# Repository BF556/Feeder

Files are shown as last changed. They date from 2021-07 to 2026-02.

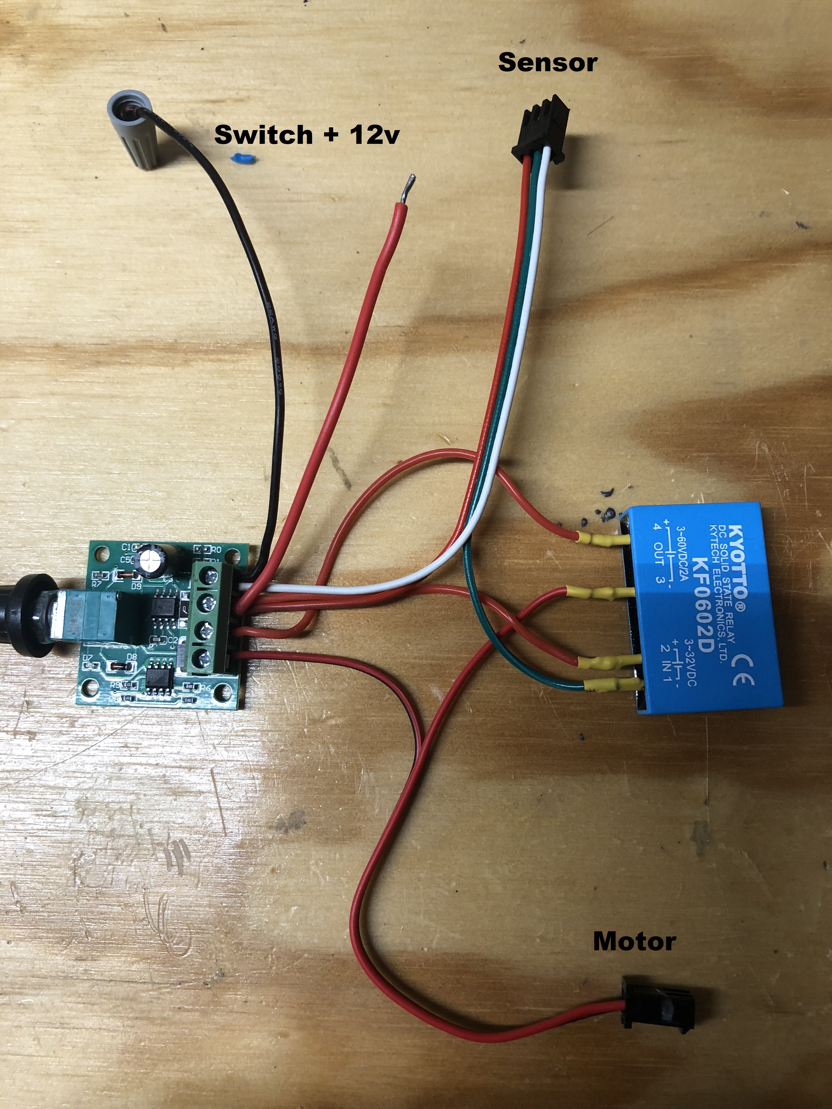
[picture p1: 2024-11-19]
Images/prox wiring.JPG

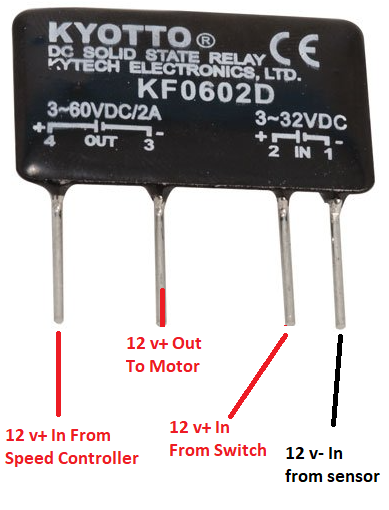
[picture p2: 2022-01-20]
Images/relay.png

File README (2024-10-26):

This work is licensed under the Creative Commons Attribution-NonCommercial 4.0 International License.

You are free to:
•	Share — copy and redistribute the material in any medium or format
•	Adapt — remix, transform, and build upon the material

Under the following terms:
•	Attribution — You must give appropriate credit, provide a link to the license, and indicate if changes were made. You may do so in any reasonable manner, but not in any way that suggests the licensor endorses you or your use.
•	NonCommercial — You may not use the material for commercial purposes.
•	No additional restrictions — You may not apply legal terms or technological measures that legally restrict others from doing anything the license permits.

To view a copy of this license, visit http://creativecommons.org/licenses/by-nc/4.0/ or send a letter to: Creative Commons, PO Box 1866, Mountain View, CA 94042, USA

Please read the manual for project details.

To download the latest design click the green "Code" button, then click "Download Zip".  In dedication of my friend Dr3wcifer.

paypal: writeus2day@yahoo.com
@bf556 on Coinbase
Bitcoin:  bc1qdez7d8wg0c6aw0pvaz97u2s23d3tlprlmmnsug
Ethereum/USDC:  0x2717F3bb693590379e953641a78d14Bf66cc5227

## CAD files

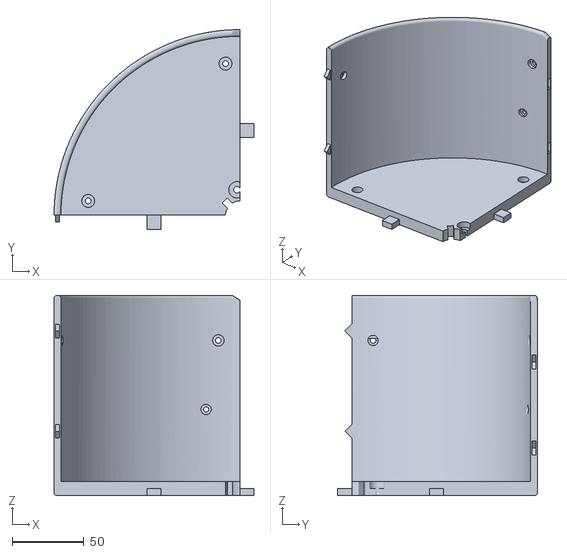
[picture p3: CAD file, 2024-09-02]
1. Main Body/Main_Body_M634JS_300mm_RB.stl
139.8 x 139.6 x 140.0

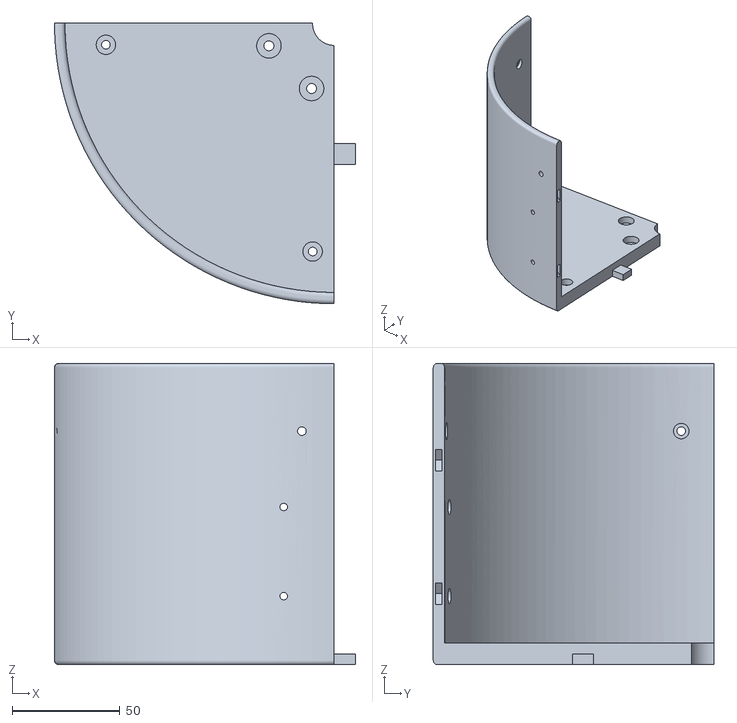
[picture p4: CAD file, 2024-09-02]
1. Main Body/Main_Body_M634JS_300mm_LB.stl
139.8 x 130.3 x 140.0

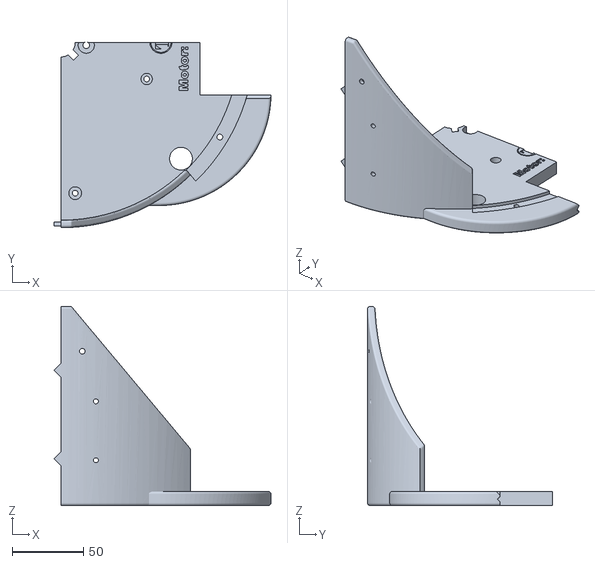
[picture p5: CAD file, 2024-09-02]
1. Main Body/Main_Body_M634JS_300mm_LF.stl
152.5 x 130.3 x 140.0

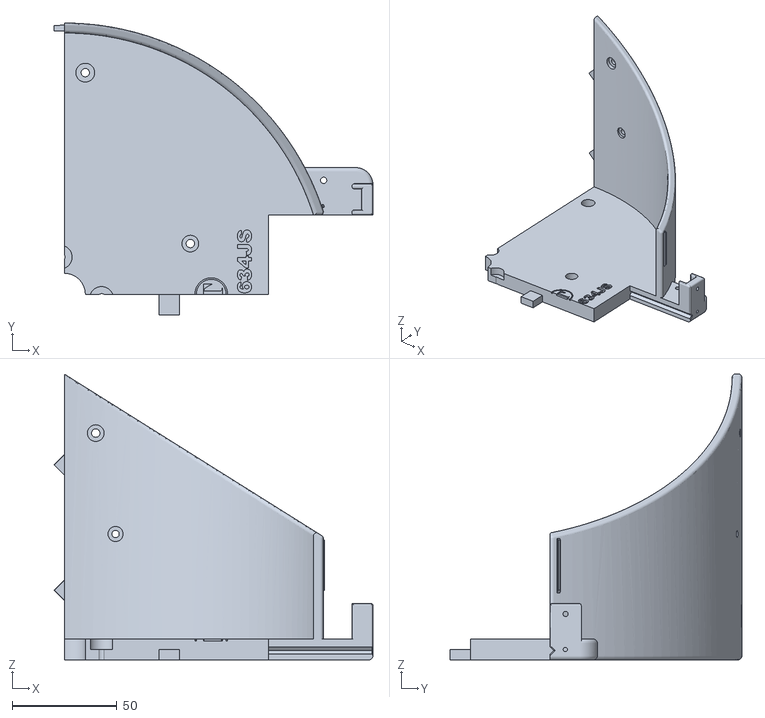
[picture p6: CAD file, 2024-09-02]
1. Main Body/Main_Body_M634JS_300mm_RF.stl
152.6 x 139.6 x 136.7

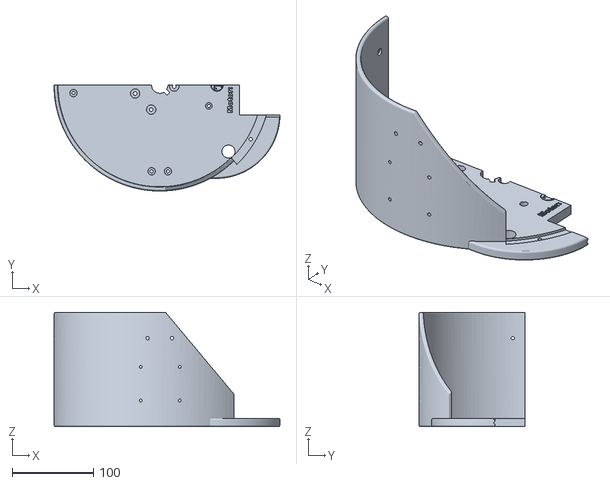
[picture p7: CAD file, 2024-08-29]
1. Main Body/Main_Body_M634JS_300mm_Left.stl
277.5 x 130.3 x 140.0

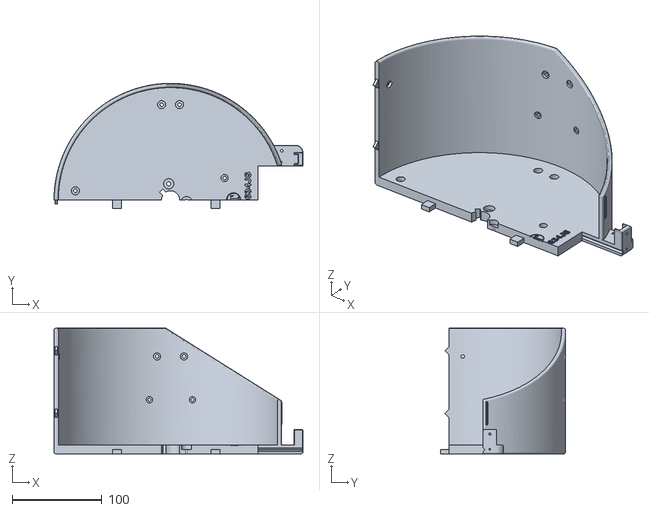
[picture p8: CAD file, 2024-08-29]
1. Main Body/Main_Body_M634JS_300mm_Right.stl
277.5 x 139.6 x 140.0

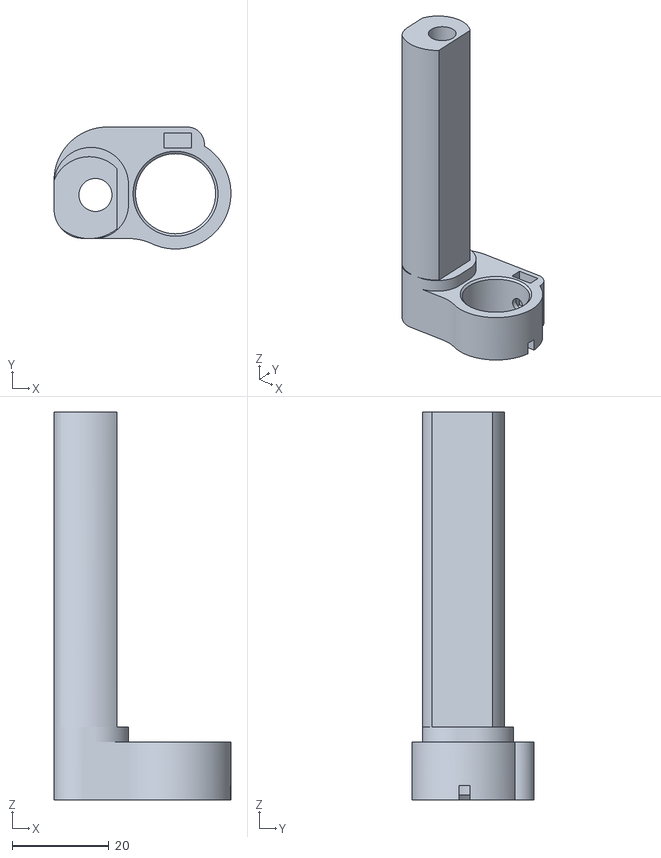
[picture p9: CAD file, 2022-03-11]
8. APP/APP_Bracket_Main.stl
36.5 x 25.1 x 80.0

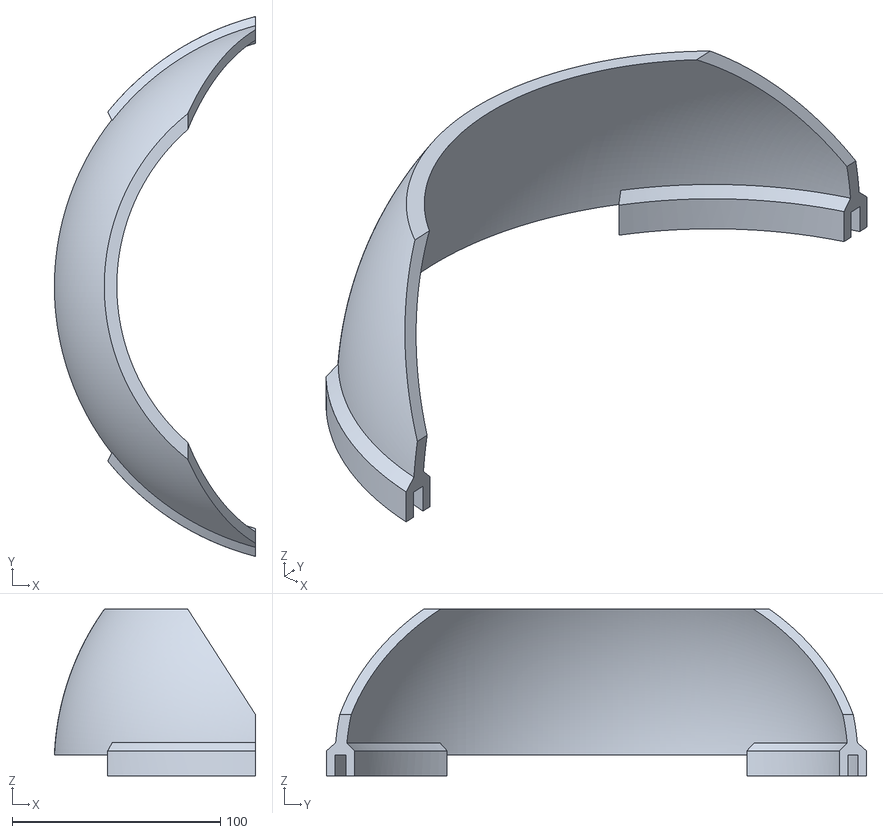
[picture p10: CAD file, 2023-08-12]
1. Main Body/Main_Body_Wall_Extender_300mm.stl
96.6 x 259.3 x 80.0

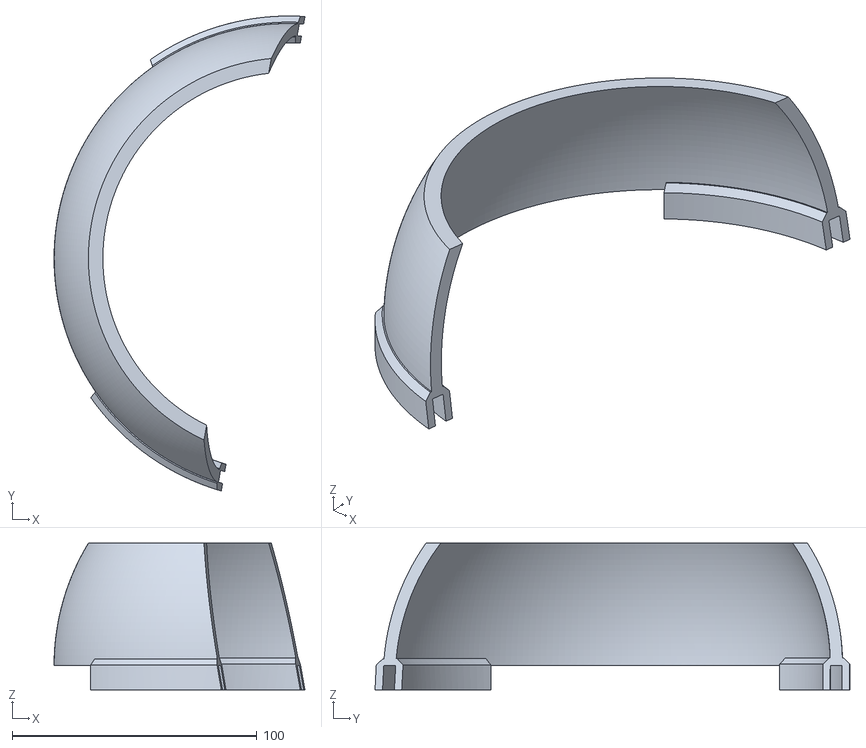
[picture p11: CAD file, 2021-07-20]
1. Main Body/Main_Body_Wall_Extender.stl
102.5 x 194.1 x 60.0

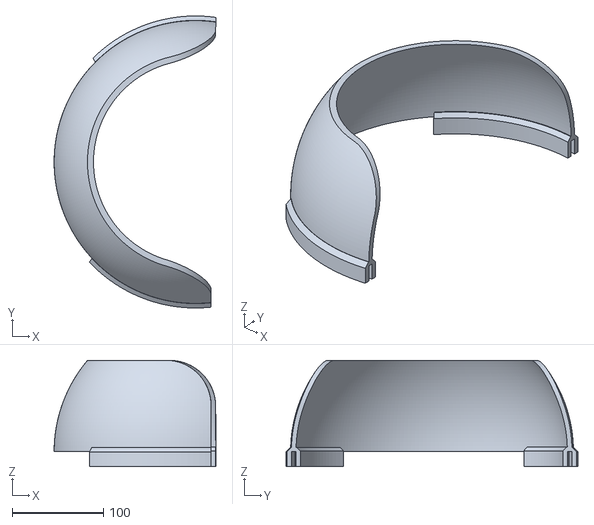
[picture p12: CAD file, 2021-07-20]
1. Main Body/Main_Body_Wall_Extender_MONGO.stl
177.3 x 320.0 x 116.5

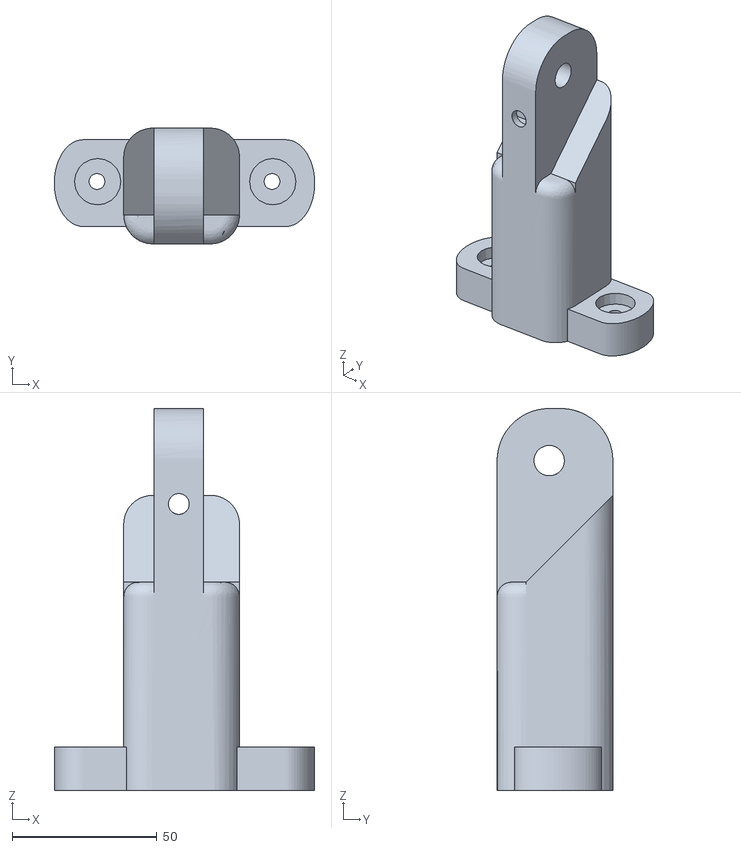
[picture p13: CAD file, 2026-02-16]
2. Mounts/Mount_Post-ASP-30x30mm.stl
90.0 x 40.0 x 132.0

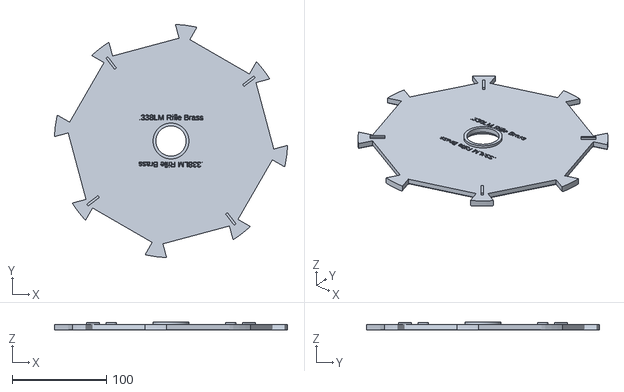
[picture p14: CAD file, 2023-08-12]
3. Collator Plates/Rifle_Brass_Collator_Plate_338LM_300mm.stl
247.2 x 247.2 x 8.50

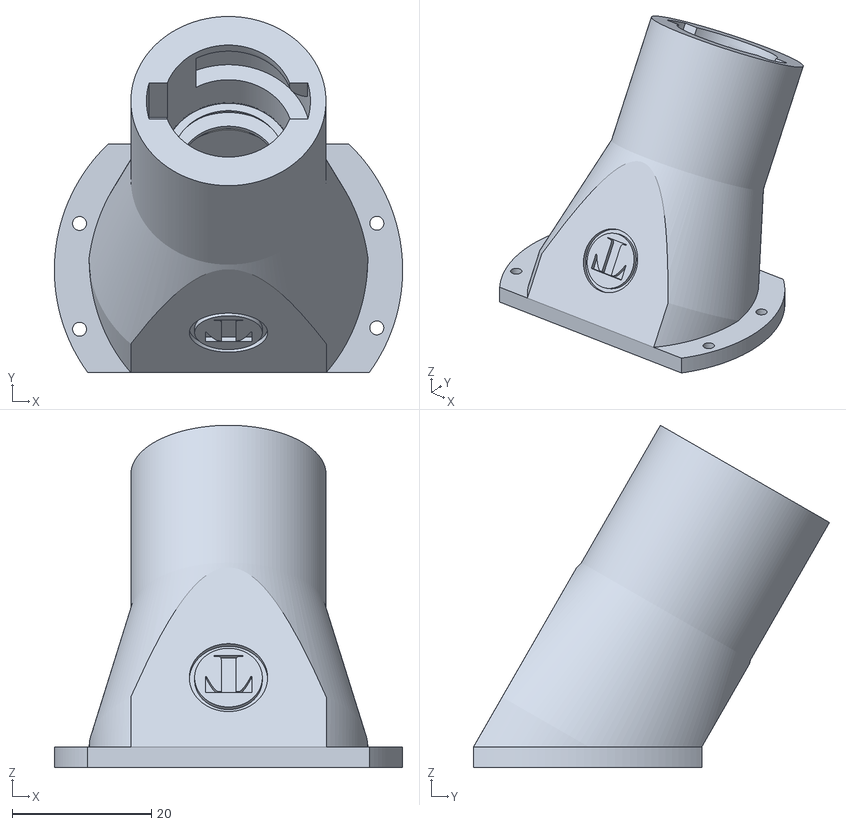
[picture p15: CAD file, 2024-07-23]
4. Slide Plates/Brass_Drop_Hole_Adapter.stl
50.0 x 51.1 x 49.1

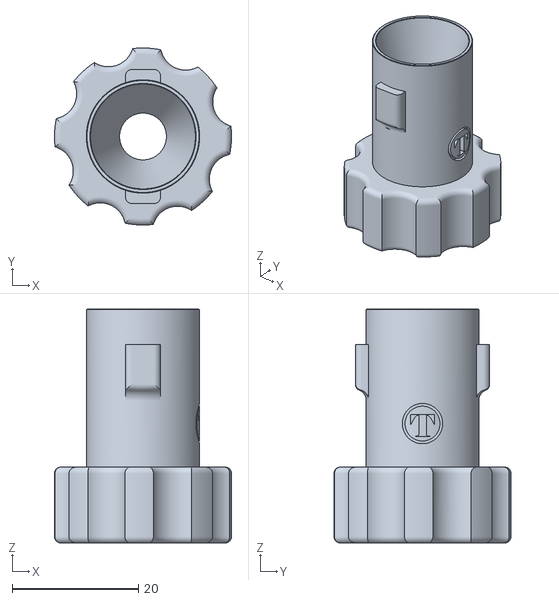
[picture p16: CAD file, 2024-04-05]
5. Adapters/Lee_Tube_Adapter_1_Funnel.stl
28.0 x 28.0 x 37.0

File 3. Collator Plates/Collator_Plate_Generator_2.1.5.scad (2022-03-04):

//*** COLLATOR PLATE GENERATOR ***///
//***   (c) AmmoMike83  ***///
//*** Mods by RedLegEd / TylerR  ***///
/*
*** INSTRUCTIONS ***
- download openSCAD http://www.openscad.org/downloads.html
- modify options
- press F5 for preview
- press F6 to render
- press F7 to export to stl
*/

//  ###########################################################
//  ##############   See Examples at bottom   #################
//  ###########################################################

//  ###########################################################
//  ###############     Options to Customize   ################
//  ###########################################################

// PLATE DIAMETER - 179.5mm(Small)/247.5mm(Medium)/297mm(Mongo)
collator_plate_d=179.5; 

// MAIN OPTIONS
description="Large Pistol Bullet (#7)"; //description
caliber=11.5; //ENTER YOUR CALIBER HERE
collator_plate_h=15; //plate height - pistol 15, rifle 18

// LONG RIFLE BULLETS
isLongRifleBullet = false; // Used for very long rifle bullets
addRamps = true; // Ramps give more angle for better feeding
squareSlotDepth = 1.5; //Depth of square bullet slot

// RIFLE BRASS PLATE OPTIONS
// Use caliber setting for hole length
isRifleBrassPlate = false; // Use with Rifle Brass  
rifleHoleWidth = 12; // Set to brass width

// PLATE OPTIONS
addPivots = false;  // Add pivots for base down brass feeding
addSlides = false;  // Add sliding slots for bullets
addSideSlides = true;  // Add sliding slots on the side of hole
slideDepth = 5.2;  // Depth of slides
slideLength = 15; // Length of slide
addRidges = true;  // Add top ridges for brass plates
ridgeCenter = true; // if false ridges align with far side of hole
ridgeAlternate = true; // Skip every other hole
ridgeHeight = 2.0; // Ridge height in mm
ridgeLength = 15; // Ridge length in mm
ridgeAngle =30; // Angle the ridges

addBevel = true;  // Add top bevel to holes
bevelSize = 1.55; // Change depth of bevel (1.3 - 1.6)
hole_multiplier=1.6; // Modify the number of holes

// SHAFT SLIP CLUTCH
useClutch = true;  // Set to true to use slip clutch

// SHAFT OPTIONS (HEX)
useHex = false;  // Set true if using hex shaft
addHexHandle = true; // Adds hex handle to top of plate
hexHandleHeight = 5; // Set height of hex handle
addHexScrewSlot = true;  // Adds slot to shaft for set screw
setScrewOnFlat = true; //  Set screw on corner or flat
hxw=12.4;  // Hex Hole Width

// SHAFT OPTIONS (STANDARD)
shaft_hole=9.5; //shaft hole
shaft_slot_length=28;
shaft_slot_width=4.5;

// Other
$fn=100; //resolution 50-100 is fine
bullet_caliber=caliber+1.0; //caliber in (mm) + 1.0 to 1.5 mm

// ####### Customize Here ########
/*
description=".300 AAC Blackout";
collator_plate_d=247.5;
caliber=36;
collator_plate_h=6;
isRifleBrassPlate = true;
rifleHoleWidth = 9;
hole_multiplier=.68;
ridgeLength = 20;
*/



//  ###########################################################
//  #############     Do Not Change Code Below   ##############
//  ###########################################################

// MAIN Routine
difference() {
union(){
                
    collator_plate();

    if(addPivots) {
        for(p=[.01:360/round(360/bullet_caliber/hole_multiplier):359]){pivot(p+15);}
    }  
  
    if(addRidges) {
        if(ridgeAlternate) {
            for(p=[0:360/round(360/bullet_caliber/hole_multiplier)*2:359]){ridges(p+15);}
        } else {
            for(p=[0:360/round(360/bullet_caliber/hole_multiplier/1):359]){ridges(p+15);}
        }
    
}
 
    if(isLongRifleBullet) {
        for(p=[0:360/round(360/bullet_caliber/hole_multiplier):359]){roundedEdge(p+15);}
    }
}

    if(isLongRifleBullet) { 
        for(p=[0:360/round(360/bullet_caliber/hole_multiplier):359]){       squareBuletHole(p+15);}
    }   
    
   
}

//  ###########################################################
module ramps(z) {
    
    z=z-2;
               translate([((collator_plate_d/2)*cos(z-caliber/2-3)),((collator_plate_d/2)*sin(z-caliber/2-3)),(collator_plate_h/2-.1)]) rotate([0,0,z+166])    prism(bullet_caliber, hole_multiplier*5, 3); 
    
}

//  ###########################################################
module squareBuletHole(z) {
    
      //Square
     translate([((collator_plate_d/2-bullet_caliber/2)*cos(z)),((collator_plate_d/2-bullet_caliber/2)*sin(z)),0]) rotate([0,0,z]) 
    cube([bullet_caliber*squareSlotDepth, bullet_caliber, collator_plate_h*2], center=true);
    
     //Bottom Bevel
     translate([((collator_plate_d/2-bullet_caliber/2+2.5)*cos(z)),((collator_plate_d/2-bullet_caliber/2+2.5)*sin(z)),-collator_plate_h/2-(bullet_caliber/14)]) rotate([45,0,z]) 
     cube([bullet_caliber*2+.5, bullet_caliber, bullet_caliber], center=true);

     translate([((collator_plate_d/2-bullet_caliber+3)*cos(z)),((collator_plate_d/2-bullet_caliber+3)*sin(z)),-collator_plate_h/2-(bullet_caliber/14)]) rotate([0,45,z]) 
      cube([bullet_caliber+2, bullet_caliber, bullet_caliber+5], center=true);
    
    // Angled Sliding Slot
     x = z-(bullet_caliber+(caliber/1)-(caliber-hole_multiplier))-2;
     translate([((collator_plate_d/2-(bullet_caliber/2-1.9))*cos(x)),((collator_plate_d/2-(bullet_caliber/2-1.9))*sin(x)),(collator_plate_h/2)+(bullet_caliber/2.5)*bevelSize/bullet_caliber+bullet_caliber+1.2]) rotate([50+hole_multiplier,1,x+7]) cube([bullet_caliber+1,10, 30+caliber*2], center=true);////////////
    
    if(isLongRifleBullet) { 
      y = z-(bullet_caliber/2)-(bullet_caliber/15);
    //translate([((collator_plate_d/2-bullet_caliber/2-30)*cos(y-3)),((collator_plate_d/2-bullet_caliber/2-30)*sin(y-3)),(collator_plate_h/2)+(bullet_caliber/3)*bevelSize]) rotate([0,-75,y])  cube([bullet_caliber+1,9, 40+caliber*2], center=true);
        
        translate([((collator_plate_d/2-bullet_caliber/2-30)*cos(y-2.2)),((collator_plate_d/2-bullet_caliber/2-30)*sin(y-2.2)),(collator_plate_h/2)+(bullet_caliber/3)*bevelSize]) rotate([0,-84,y])  cylinder(d2=bullet_caliber/2, d1=bullet_caliber-0,h=54.1,center=true);
        
        
    }
}

//  ###########################################################
module pivot(p){
    cube = 4;
    translate([((collator_plate_d/2-bullet_caliber-1)*cos(p)),((collator_plate_d/2-bullet_caliber-1)*sin(p)),-1]) rotate([0,60,p]) cube ([cube,1.5,cube], center=true);}
    
 //  ###########################################################   
module ridges(p) {

    if(isRifleBrassPlate) { 
        p=p+360/round(360/bullet_caliber/hole_multiplier)/2;
         translate([((collator_plate_d/2-ridgeLength/2-12)*cos(p)),((collator_plate_d/2-ridgeLength/2-12)*sin(p)),collator_plate_h/2]) rotate([-ridgeAngle,-90,p]) cube ([ridgeHeight*2,2.5,ridgeLength], center=true); 
        
        } else {
            
        if(ridgeCenter) {
             p=p+(360/round(360/bullet_caliber/hole_multiplier)/2)-.5;
         translate([((collator_plate_d/2-ridgeLength/2-3)*cos(p)),((collator_plate_d/2-ridgeLength/2-3)*sin(p)),collator_plate_h/2]) rotate([-ridgeAngle,-90,p]) cube ([ridgeHeight*2,2.5,ridgeLength], center=true); 
        
        }  else {
            p = p+(bullet_caliber/2)-(bullet_caliber/15)+.5;
            translate([((collator_plate_d/2-ridgeLength/2-.3)*cos(p)),((collator_plate_d/2-ridgeLength/2-.3)*sin(p)),collator_plate_h/2]) rotate([0,-90,p]) cube ([ridgeHeight*2,2.5,ridgeLength], center=true); 
        }
    }
}  

//  ###########################################################
module roundedEdge(p) {

     z = p-(bullet_caliber+(caliber/1.0)+0);
    
    union() {
     difference(){
        union() {

     mf = 2-caliber/15;       
             translate([((collator_plate_d/2-bullet_caliber/2-mf)*cos(z)),((collator_plate_d/2-bullet_caliber/2-mf)*sin(z)),bullet_caliber/2-caliber-3]) rotate([-12,90,z]) cylinder(d=bullet_caliber*4.6,h=bullet_caliber+5.9, center=true);
            
        }

        translate([((collator_plate_d/2-bullet_caliber/2)*cos(z-6.5)),((collator_plate_d/2-bullet_caliber/2)*sin(z-6.5)),bullet_caliber/2-9]) rotate([-15,90,z]) cube ([bullet_caliber*5,bullet_caliber*3+10,bullet_caliber*4],center=true);

      translate([0, 0, -collator_plate_h-10 ]) cylinder(d=collator_plate_d+10,h=collator_plate_h+20, center=true) ;
        
         translate([0, 0, collator_plate_h ])  cylinder(d=collator_plate_d+10,h=collator_plate_h, center=true) ;

    }
      // ##### LONG RIFLE ######
            if(isLongRifleBullet && addRamps) {
           for(z=[0:360/round(360/bullet_caliber/hole_multiplier):359]){ramps(z+15);}
         }
    }
}
    
//  ###########################################################
module collator_plate(){
    difference(){
        //plate
        union() {
            
            
            cylinder(d=collator_plate_d,h=collator_plate_h, center=true) ;
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

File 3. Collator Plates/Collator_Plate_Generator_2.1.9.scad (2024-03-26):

//*** COLLATOR PLATE GENERATOR ***///
//***   (c) AmmoMike83  ***///
//*** Mods by RedLegEd / TylerR  ***///
/*
*** INSTRUCTIONS ***
- download openSCAD http://www.openscad.org/downloads.html
- modify options
- press F5 for preview
- press F6 to render
- press F7 to export to stl
*/

//  ###########################################################
//  ##############   See Examples at bottom   #################
//  ###########################################################

//  ###########################################################
//  ###############     Options to Customize   ################
//  ###########################################################

// PLATE DIAMETER - 179.5mm(Small)/247.5mm(Medium)/297mm(Mongo)
collator_plate_d=179.5; 

// MAIN OPTIONS
description="Large Pistol Bullet (#7)"; //description
caliber=11.5; //ENTER YOUR CALIBER HERE
collator_plate_h=15; //plate height - pistol 15, rifle 18
hole_multiplier=1.6; // Modify the number of holes

// PLATE OPTIONS
addBevel = true;  // Add top bevel to holes
bevelSize = 1.55; // Change depth of bevel (1.3 - 1.6)

// RIFLE BRASS PLATE OPTIONS
// Use caliber setting for hole length
isRifleBrassPlate = false; // Use with Rifle Brass  
rifleHoleWidth = 12; // Set to brass width

// Ridge Options
addRidges = true;  // Add top ridges for brass plates
ridgeCenter = true; // if false ridges align with far side of hole
ridgeAlternate = true; // Skip every other hole
ridgeAlternateNum = 2; // Set how ofter the ridges occur
ridgeHeight = 2.0; // Ridge height in mm
ridgeLength = 15; // Ridge length in mm
ridgeWidth = 2.5; // Ridge width in mm
ridgeAngle = 30; // Angle the ridges
ridgePosition = 0; // Position of the ridges
ridgeInsidePosition = 3; // Inside position of the ridges

// Slide Options
addSlides = false;  // Add sliding slots for bullets
//slideDepth = 1;  // Depth of slides
//slideLength = 50; // Length of slides
//slideSize = 1; // Diameter of slides
//slidePosition = 0;  //Position of slides
//slideAngle = 0;

addSideSlides = true;  // Add sliding slots on the side of hole
slideDepth = 2.0;  // Depth of slides
slideLength = 12; // Length of slides
slideSize = 1.0; // Diameter of slides
slidePosition = -6;  //Position of slides
slideAngle = 10;
slideAngle2 = 0;

// Ramp Options
addRamps = false; // Ramps give more angle for better feeding
rampHeight = 3.0;
rampLength = 7;
rampWidth = 3.5;
rampPosition = .9;
rampAngle = 4.5;
rampTopStart = 0;
rampTopLength = 1;
rampTopWidth = 2;
rampW0 = -.7;
rampW1 = .34;

// Pivot Options
addPivots = false;  // Add pivots for base down brass feeding
pivotPosition = 15;
pivotSize = .6;
pivotHeight = 1.2;
pivotWidth = 1;

// LONG RIFLE BULLETS
isLongRifleBullet = false; // Used for very long rifle bullets
squareSlotDepth = 1.5; //Depth of square bullet slot
roundedEdgeHeight = 4.9;
roundedEdgeWidth = 4.5;
roundedEdgePosition = 0;
roundedEdgeCut = 6.9;
roundedEdgeAngle = 0;
roundedEdgeSlotHeight = 0;

angledSlotHeight = 4.57;
angledSlotWidth = 1.7;
angledSlotLength = 0;
angledSlotPosition = 5.4;
bottomBevelDepth = 1.5;
bottomBevelHeight1 = -1;
bottomBevelHeight2 = 0;

// SHAFT SLIP CLUTCH
useClutch = true;  // Set to true to use slip clutch

// SHAFT OPTIONS (HEX)
useHex = false;  // Set true if using hex shaft
addHexHandle = true; // Adds hex handle to top of plate
hexHandleHeight = 5; // Set height of hex handle
addHexScrewSlot = true;  // Adds slot to shaft for set screw
setScrewOnFlat = true; //  Set screw on corner or flat
hxw=12.4;  // Hex Hole Width

// SHAFT OPTIONS (STANDARD)
shaft_hole=9.5; //shaft hole
shaft_slot_length=28;
shaft_slot_width=4.5;

// Other
$fn=100; //resolution 50-100 is fine
bullet_caliber=caliber+1.0; //caliber in (mm) + 1.0 to 1.5 mm

// ####### Customize Here ########

description="Small Brass Base Up"; 
collator_plate_d=248.0;
caliber=10.5;
collator_plate_h=20; 

addPivots = true;
pivotPosition = 15;
pivotSize = 4.9;
pivotHeight = 1.2;
pivotWidth = 1.4;

addSlides = false;
hole_multiplier=1.1;
bevelSize = 1.65;
ridgeAlternate = true;
ridgeLength = 15;
ridgeAngle = 30;
slideDepth = 4.5;
slideLength = 15; 

addSideSlides = true;
slideDepth = 1.0; 
slideLength = 18; 
slideSize = 1.5;
slidePosition = -4.0; 
slideAngle = -15;
slideAngle2 = -6;



//  ###########################################################
//  #############     Do Not Change Code Below   ##############
//  ###########################################################

// MAIN Routine  
//collator_plate();

union(){
    difference() {
        union(){
            collator_plate();
            if(addRidges && ridgeAlternate) {
                for(p=[0:360/round(360/bullet_caliber/hole_multiplier)*ridgeAlternateNum:359]){ridges(p+15);} 
            }
            for(z=[0:360/round(360/bullet_caliber/hole_multiplier):359]){
                if(addRidges && !ridgeAlternate) {ridges(z+15);} 
                if(isLongRifleBullet) {roundedEdge(z+15);}
                if(addRamps) {ramps(z+15);}
            }   
        }
        if(isLongRifleBullet) {
            for(z=[0:360/round(360/bullet_caliber/hole_multiplier):359]){
                squareBuletHole(z+15);
            }
        }
    }   
    if(addPivots) {
        for(z=[0:360/round(360/bullet_caliber/hole_multiplier):359]){
            pivot(z+pivotPosition);
        }
    }
}


//  ###########################################################
module ramps(z) {
    
    z=z-rampPosition;
    
    translate([((collator_plate_d/2)*cos(z-caliber/2-3)),((collator_plate_d/2)*sin(z-caliber/2-3)),(collator_plate_h/2)]) 
        rotate([0,0,z+166+rampAngle])    
        prism(rampLength, rampWidth, rampHeight); 
    
}

//  ###########################################################
module squareBuletHole(z) {

      //Square
     translate([((collator_plate_d/2-bullet_caliber/2)*cos(z)),((collator_plate_d/2-bullet_caliber/2)*sin(z)),0]) rotate([0,0,z]) 
        cube([bullet_caliber*squareSlotDepth, bullet_caliber, collator_plate_h*3], center=true);
    
     //Bottom Bevel
     translate([((collator_plate_d/2-bullet_caliber/2+2.4)*cos(z)),((collator_plate_d/2-bullet_caliber/2+2.4)*sin(z)),-collator_plate_h/2+bottomBevelHeight1]) rotate([45,0,z]) 
        cube([bullet_caliber*bottomBevelDepth, bullet_caliber, bullet_caliber], center=true);

 //Bottom Bevel
   //  translate([((collator_plate_d/2-bullet_caliber/2+2.4)*cos(z)),((collator_plate_d/2-bullet_caliber/2+2.4)*sin(z)),-collator_plate_h/2]) rotate([45,0,z*1.5]) 
    //    cube([bullet_caliber*bottomBevelDepth, bullet_caliber, bullet_caliber], center=true);

//translate([((collator_plate_d/2-bullet_caliber+3)*cos(z)),((collator_plate_d/2-bullet_caliber+3)*sin(z)),-collator_plate_h/2-(bullet_caliber/20)]) rotate([0,45,z])


     translate([((collator_plate_d/2-bullet_caliber+3)*cos(z)),((collator_plate_d/2-bullet_caliber+3)*sin(z)),-collator_plate_h/2+bottomBevelHeight2]) rotate([0,45,z]) 
       cube([bullet_caliber+.5, bullet_caliber-.1, bullet_caliber+5], center=true);
    
    // Angled Sliding Slot
     //x = z-(bullet_caliber+(caliber/1)-(caliber-hole_multiplier))-2;
    x = z + angledSlotPosition ;
     translate([((collator_plate_d/2-(bullet_caliber/2-2.0))*cos(x)),((collator_plate_d/2-(bullet_caliber/2-2.0))*sin(x)),(collator_plate_h/2)+(bullet_caliber/2.5)*bevelSize/bullet_caliber+bullet_caliber+angledSlotHeight]) rotate([40+hole_multiplier,-1,x+5])
        cube([bullet_caliber+angledSlotWidth,10, 30+caliber+angledSlotLength*2], center=true);////////////

    // Add slide slot
      if(addSlides) {
        
        p = z + slidePosition;     
        translate([((collator_plate_d/2-bullet_caliber/2-25)*cos(p)),((             collator_plate_d/2-bullet_caliber/2-25)*sin(p)),collator_plate_h/2-slideDepth+5])    rotate([0,-90+slideAngle,p-slideAngle2])
         
        cylinder(d2=bullet_caliber/2, d1=bullet_caliber+slideSize,h=slideLength,center=true);

    }
          
}
//  ###########################################################
module roundedEdge(p) {

     z = p-(bullet_caliber+(caliber/1.0))+roundedEdgePosition;

difference(){
  union() {
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

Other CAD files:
6. Drop Tubes/Drop_Tube_9mm.stl
7. Bullet Feed Dies/Feed_Die_6.5G_Insert.stl
8. APP/APP_Spring_APP_Insert_XL.stl
1. Main Body/Drop_Hole_Adapter.stl
1. Main Body/Drop_Hole_Adapter_Angled.stl
1. Main Body/Drop_Hole_Adapter_Angled_Body.stl
1. Main Body/Drop_Hole_Adapter_Angled_Slide.stl
1. Main Body/Drop_Hole_Adapter_Small_Right.stl
1. Main Body/Drop_Hole_Spacer_Long.stl
1. Main Body/Drop_Hole_Spacer_Short.stl
1. Main Body/Electronics_Box_Large.stl
1. Main Body/Electronics_Box_Large_Lid.stl
1. Main Body/Electronics_Box_Large_Template.stl
1. Main Body/Electronics_Box_Small.stl
1. Main Body/Electronics_Box_Small_300.stl
1. Main Body/Electronics_Box_Small_Bottom.stl
1. Main Body/Electronics_Box_Small_Bottom2.stl
1. Main Body/Electronics_Box_Small_Lid.stl
1. Main Body/Electronics_Box_Small_MONGO.stl
1. Main Body/Electronics_Box_Small_Right.stl
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

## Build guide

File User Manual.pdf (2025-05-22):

# The HomeFree Universal Reloading System

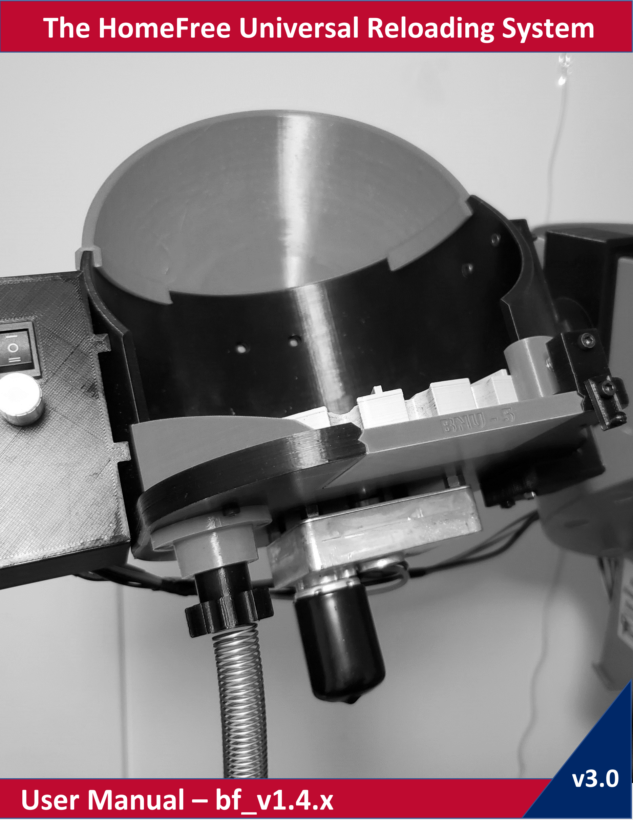
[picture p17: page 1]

v3.0

# User Manual – bf_v1.4.x

## Manual Contents

ACKNOWLEDGEMENTS | ERROR! BOOKMARK NOT DEFINED.

## PREFACE

## INTRODUCTION

Before 3D printing or engaging in this project’s dedicated thread (http://castboolits.gunloads.com/showthread.php?354324-Making-that-Bullet-Collator) on Cast Boolits, please read this user manual in its entirety as it combines the cumulative experience of numerous individuals. Ensure that the downloaded (https://www.dropbox.com/sh/xczanojq6ly3jqa/AAA5yU7iMbX_N46aC9SVfdjza) project build matches, or is higher, than the one listed on the cover page of this manual. If you would like to leave feedback on this manual, please do so here. (https://www.dropbox.com/sh/sz1o53q1a9hn4vn/AABTmmivEKmxgWxunXAH2t7Ta/User%20Manual%20Feedback%20and%20Suggestions.xlsx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)

## 3D PRINTER

A reliable 3D printer with a minimum bed size of 210mm x 210mm x 140mm, like an Ender 3, will suffice for this project. A properly calibrated 3D printer is mandatory as many parts have tight tolerances and will take hours to print. Here is a superb calibration video (https://www.youtube.com/watch?v=rp3r921DBGI) to watch before printing anything; pay close attention to the sections on frame check, (https://www.youtube.com/watch?v=rp3r921DBGI&t=166s) E-steps, (https://www.youtube.com/watch?v=rp3r921DBGI&t=422s) flow rate (https://www.youtube.com/watch?v=rp3r921DBGI&t=503s) and retraction. (https://www.youtube.com/watch?v=rp3r921DBGI&t=669s)

## FILAMENT

We recommended using PLA/PLA+ from reputable brands like Hatchbox, Overture, Sunlu, E-Sun, AMZ3D.

## TEMPERATURES

Print temperature will vary based on filament brand so feel free to experiment a little. We recommend a nozzle/bed temperature of 210˚C/60˚C as a starting point.

## NOZZLE SIZE

We recommend printing every part with a 0.4mm nozzle. While this will increase print times, it will also ensure quality parts are printed.

## PRINT SPEED

Faster prints often lead to dimensional accuracy issues, artifacts and failed prints. We recommend infill, wall and initial layer speeds of 50, 25 and 20mm/s, respectively.

## LAYER HEIGHT/INFILL/SUPPORTS/WALLS/ADHESION

All parts have their recommended print settings listed in this manual. We highly recommend following them as they have proven to yield the best quality prints.

## SLICER

We recommend Cura’s free slicing software as it has tons of print settings to play around with. Regardless, Cura’s default Standard Quality (0.2mm Layer Height) and Super Quality (0.12mm Layer Height) will suffice.

## SUB-PROJECTS

## BRASS AND BULLET COLLATOR OVERVIEW

Here is a labelled diagram of the main body with all its salient features:
A. Ramp Housing
Houses various flipping ramps.
B. Flipper Housing
Houses the flipper and sweepers.
C. Drop Hole
Hole through which brass/bullets fall.
D. Motor Mount
Secures motor to the main body.
E. Electronics Box Mount
Secures electronics box.
F. Rear Mount
Secures collator for pole mounting.
G. Right Side Mount
Secures collator for Dillon mounting.
H. Slide Plate Housing
Houses various slide plates.

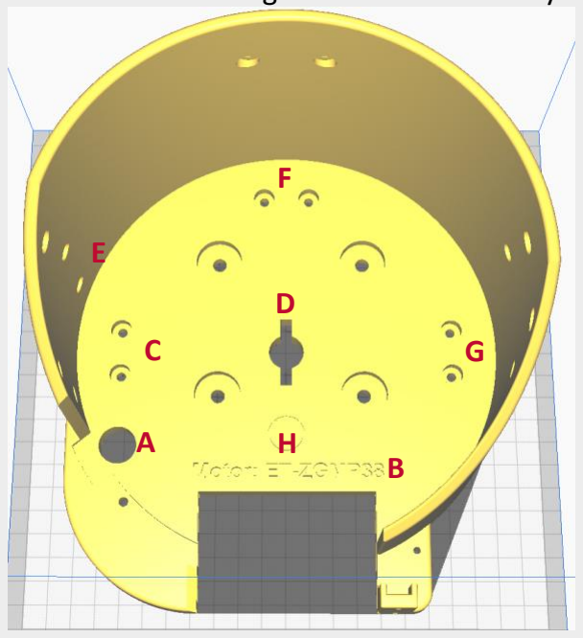
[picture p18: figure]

The following videos demonstrate all the operational capabilities of the brass and bullet collator:
- Nose up bullet collation (small bullet (https://vimeo.com/517852693)/long bullet) (https://vimeo.com/517852597)
- Nose down bullet collation (small bullet (https://vimeo.com/517852389)/long bullet) (https://vimeo.com/517852526)
- Base up brass collation (small brass) (https://vimeo.com/517852272)
- Base down brass collation (small brass (https://vimeo.com/517852848)/large brass) (https://vimeo.com/517852748)

## MONGO BRASS COLLATOR OVERVIEW

The MONGO collator has been specifically designed for large scale brass collation. Most parts from the above sub-project are compatible with the MONGO sub-project, but parts specific to this sub-project have the word MONGO attached to their filename. It should be noted that some MONGO parts require a 3D printer with a large print bed (350mm x 350mm), like an Ender 5 Plus. Here are some videos (small brass (https://vimeo.com/539431234)/large brass) (https://vimeo.com/539792171) demonstrating the operational capabilities of the MONGO brass and bullet collator.

## BULLET FEED DIES OVERVIEW

The caliber specific bullet feed dies interface directly below the drop tubes and thread directly into press toolhead with 7/8”-14 threading. Here is a video (https://vimeo.com/517848766) showing the bullet feed die in action.

## LEE APP ACCESSORIES OVERVIEW

The Lee APP accessories improve press reliability and implement the quick caliber change system for both brass and bullets. They can also work with the brass and bullet collator for super fast component processing. Here is a video (https://vimeo.com/517852456) showing the accessories in action.

## NON-3D PRINTED PARTS

Here is a comprehensive list of necessary parts by sub-project:

## BRASS AND BULLET COLLATOR

- Motor – the collator bases work with the following motors:
- 634JS (https://www.amazon.com/Greartisan-Self-Locking-Reversible-Reduction-Electric/dp/B07YBXMTWC) (recommended)
- ETZGMP38 (https://www.grainger.com/product/DAYTON-DC-Gearmotor-12VDC-52JE51)
- Switch (https://www.amazon.com/gp/product/B08Q3WJW8Q/ref=ppx_od_dt_b_asin_title_s00?ie=UTF8&psc=1) – a standard switch to power the collator unit on and off.
- Speed Controller (https://www.amazon.com/gp/product/B08XQ22F47/ref=ppx_yo_dt_b_search_asin_title?ie=UTF8&psc=1) – a motor speed controller circuit to adjust the collator plate speed.
- Power Supply (https://www.amazon.com/gp/product/B07RGHBLGC/ref=ppx_yo_dt_b_asin_title_o05_s02?ie=UTF8&psc=1) – a 12V power supply to power all the electronics.
- Female Adapter Plug (https://www.amazon.com/gp/product/B07MJ4YWQ8/ref=ppx_yo_dt_b_search_asin_title?ie=UTF8&th=1) – an adapter plug to plug in the power supply.
- JST Motor Connectors (https://www.amazon.com/gp/product/B07HN4HXZW/ref=ppx_yo_dt_b_search_asin_title?ie=UTF8&psc=1) – a set of JST connectors to connect the motor to the electronics box.
- JST Sensor Connectors (https://www.amazon.com/gp/product/B075K4HLTQ/ref=ppx_yo_dt_b_search_asin_title?ie=UTF8&th=1) – a set of JST connectors to make a wire harness for the drop tube sensors.
- Screws/Washers/Nuts (https://www.amazon.com/NINDEJIN-Socket-Screws-1060pcs-Assortment/dp/B07PHYJ8BB) – a hex nut kit with various sized bolts.
- Springs (https://www.amazon.com/dp/B0BG5W6M4Z?ref_=cm_sw_r_apan_dp_BYGXHAW4EADZJGAMCJ7N) – a spring kit with various sized springs.
- Sensors – select the parts based on the drop tube system being implementing:
- Proximity Sensor Drop Tube System
- Proximity Sensor (https://www.amazon.com/gp/product/B00TXXH4OA/ref=ppx_yo_dt_b_asin_title_o01_s00?ie=UTF8&psc=1) – a 14mm detection range normally closed (NC) inductive proximity sensor.
- Proximity Sensor (https://www.ebay.com/itm/333737317263) (Ebay) – Same as above but less expensive, slow delivery.
- Relay (https://www.amazon.com/gp/product/B00B888WVC/ref=ppx_yo_dt_b_asin_title_o00_s00?ie=UTF8&psc=1) – a 2A solid state relay.
- Photoswitch Drop Tube System (Legacy)
- Photoswitch (https://www.amazon.com/gp/product/B00XAH7DTQ/ref=ppx_yo_dt_b_asin_title_o01_s00?ie=UTF8&psc=1) – a 12V photoswitch relay circuit with a photosensor.
- LED (https://www.amazon.com/50pcs-Ultra-Bright-Diodes-Light-White/dp/B01MYYUS2R) – a 12V LED; white LEDs work best.
- Micro Switch Drop Tube System (Legacy)
- Micro Switch (https://www.amazon.com/Twidec-Straight-Switch-Action-KW11-3Z03/dp/B07P11JG8K) – a micro switch.
- Micro Switch (https://www.digikey.com/en/products/detail/honeywell-sensing-and-productivity-solutions/V7-5F17D8-336/1248546) – a more sensitive switch for light brass; trim the sides of the arm.
- Spring Tubes – choose from any of the following sizes and styles of spring tubes:
- Small/Large Spring Tube (https://www.doublealpha.biz/us/mrbulletfeeder-output-spring-and-extension-adaptor) – for feeding small rifle and large caliber brass and bullets.
- Extra Large Spring Tube (https://www.doublealpha.biz/us/double-alpha-output-chute-and-spring) – for more reliable feeding of large caliber brass and bullets.
- Multi-Diameter Spring Tube (https://tinyurl.com/ynmrh72e) – an alternative to the above spring tubes.
- Multi-Diameter Spring Tube (https://www.mcmaster.com/coil-springs/extension-spring-stock-6/) (USA) – an alternative to the above spring tubes
- Multi-Diameter Spring Tube (https://a.co/d/aAxyJWb) (USA) – another option from Amazon
- Hex Couplers (https://www.amazon.com/uxcell-Coupler-Coupling-Flexible-Connector/dp/B08M45D6F2) – a hex motor coupler alternative to pinning the motor shaft.

## BULLET FEED DIE

- Ball Bearings (https://www.amazon.com/uxcell-3-5mm-Bearing-Chromium-Precision/dp/B081SQZR62) – a set of 3.5mm ball bearings.
- Elastic bands, hooked springs (https://www.mcmaster.com/9654K964/) or O-rings.

## LEE APP ACCESSORIES

Non-3D printed parts are not required for this sub-project.

## 3D PRINTED PARTS

The project folders are numbered to reflect the build order of this manual as follows:
1. Main Body
2. Mounts
3. Collator Plates
4. Slide Plates
5. Adapters
6. Drop Tubes
7. Bullet Feed Dies
8. APP
9. Contributors - this folder contains experimental files and therefore not documented. Images – this folder contains reference images.

## IMPORTANT – PLEASE READ!

Given that this project contains over 200 files, we strongly recommend using the Parts Generator application to ensure that the correct parts are printed. While the app is not a substitute for this manual, most of the required project parts can be acquired through it. The remaining parts, which are optional and/or build specific, can be determined via this manual.

## STEP 1 – COLLATOR MAIN BODY

Part | Layer Height | Infill | Supports | Walls | Adhesion
Main Body | 0.2mm | 30% | None | 4 | None
Electronics Box | 0.2mm | 10% | None | 2 | None
All Other | 0.12mm | 10-20% | None | 2 | None

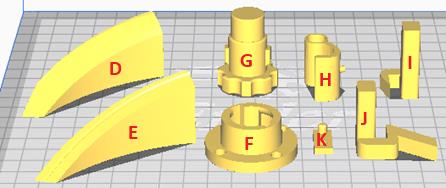
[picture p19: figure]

Main Body Folder
Part | STL File | Description
A-B | Main_Body_X | All files labelled Main_Body are used to create the collator main body.
C-X | Electronics_Box | All files labelled Electronics_Box are used to create the electronics box.
D | Ramp | This ramp rotates bullets and mounts to the ramp housing with 1 screw; this part is only used for nose up/down bullet collation.
E | Ramp_Brass_Base_Up | This ramp rotates brass and mounts to the ramp housing with 1 screw; this part it is only used for base up brass collation.
F | Drop_Hole_Adapter | This adapter allows for the quick attachment of the spring tube and mounts to the bottom of the main body’s drop hole with 4 screws.
G | Drop_Hole_Plug | This plug screws into the drop hole adapter and disables it; this part is only used for base up/down brass and nose down bullet collation.
H Flipper | | This spring-loaded flipper knocks misaligned bullets and mounts onto the flipper housing with 1 screw; a screw located on the front of the flipper housing holds the spring in place.
I | Sweeper | This sweeper arm knocks misaligned bullets and clamps onto the flipper housing; this part is only used for base up brass and long bullet collation.
J | Sweeper_Long | This sweeper arm knocks misaligned brass and clamps onto the flipper housing; this part is only used for base down rifle brass collation.
K | Slide_Plate_Latch | This latch secures slide plates and screws onto the front of the slide plate housing with 1 screw; this is an optional part.

MAIN BODY PARTS

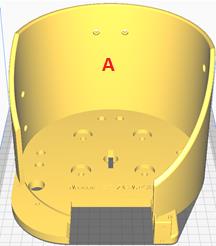
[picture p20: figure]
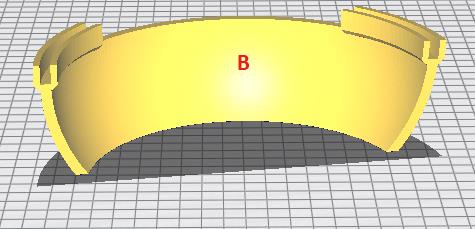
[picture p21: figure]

Part A is the collator main body and is based on the motor type being used. It requires the most time to print so ensure that the 3D printer is calibrated correctly before printing.

Part B is an optional part that friction fits to the top lip of the collator and increases collator capacity while preventing component spillage.

ELECTRONICS BOX PARTS
There are two electronics box sizes to choose from, part C-1, small and large. While the large electronics box works with any configuration of parts, we recommend the small electronics box with the proximity sensor drop tube system. The lid, part C-2, for the electronics box slides into the rear opening.

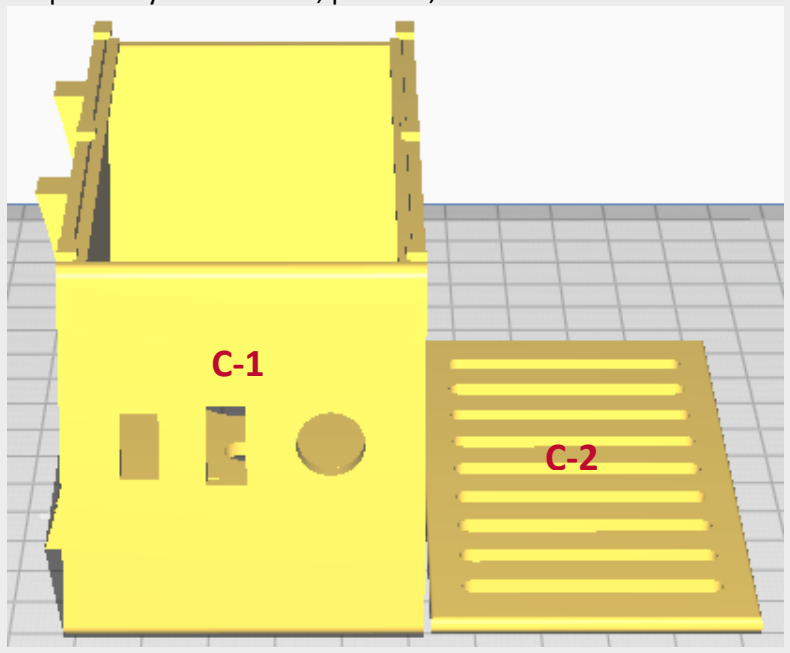
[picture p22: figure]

Files that are labelled Electronics_Box_X_Template do not have any component cut outs and allow for customization through software like Tinkercad. (https://www.tinkercad.com/)

## STEP 2 – COLLATOR MOUNTS

Part | Layer Height | Infill | Supports | Walls | Adhesion
All | 0.2mm | 30% | None | 4 | None

Mounts Folder
Part | STL File | Description
A-B | Mount_Dillon_Hang_X | These files are used to create a Dillon casefeeder mount.
C-D | Mount_Post_X | These files are used to create mounts that secure to vertical posts.
E | Mount_Square_X | These files are used to create mounts that secure to horizontal posts.
F | Thumb_Screw | This thumb screw cover is used for the adjustment screw option.

The brass and bullet collator can be mounted to a Dillon casefeeder or a circular/square post that is 1” in diameter. A 45˚ collator tilt is normally optimal, but this can vary by brass or bullet caliber.

DILLON CASEFEEDER MOUNT
A 3/8” x 1” hex bolt, washer and nut goes through the parts A and B to
control collator tilt. Be sure to insert the hex bolt before screwing the Dillon hang base to the main body. Part A mounts to the right side of the collator while part B slips over the top lip of the Dillon casefeeder.

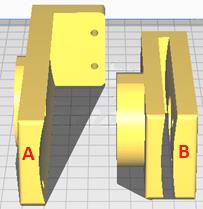
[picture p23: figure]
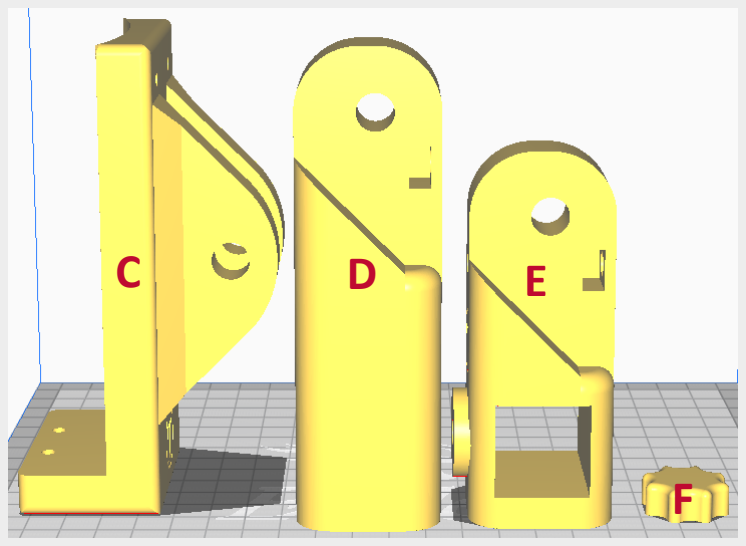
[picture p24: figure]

VERTICAL & HORIZONTAL POST MOUNTS
A 3/8” x 2 1/4” hex bolt, washer and nut goes through part C and parts D/E to control collator tilt. Part C mounts to the rear of the collator while part D slips over the top of the post being used; part D comes in two styles, one for circular posts and the other for square posts. As an alternative mounting style, part E is designed for mounting to a square horizontal post.

For those making regular changes to the collator tilt, we suggest using the adjustment screw option. A 1/4” bolt and nut can be used with parts D/E to provide an alternative to the friction fit approach of using only a hex bolt. We also recommend using part F to act as a thumb screw for the adjustment screw; see the figure on the right.

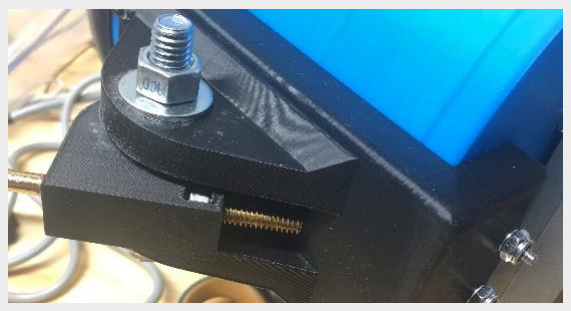
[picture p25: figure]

## STEP 3 – COLLATOR PLATES

Part | Layer Height | Infill | Supports | Walls | Adhesion
All Other | 0.2mm | 10% | None | 2 | None
Slip_Clutch_X | 0.2mm | 50% | None | 4 | None

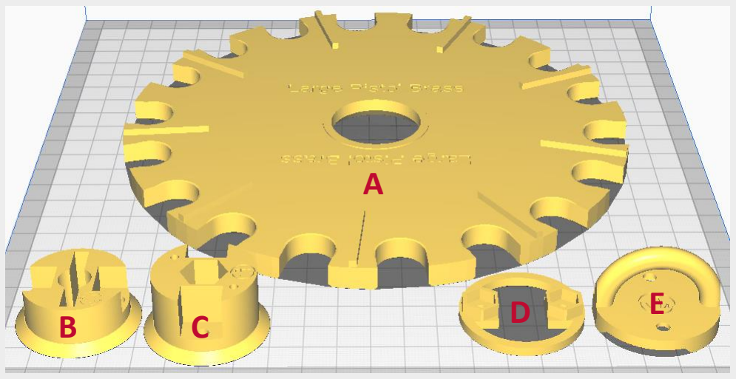
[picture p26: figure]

Collator Plates Folder
Part | STL File | Description
A X_Collator_Plate_X | | All files labelled Collator_Plate are used to create brass/bullet collator plates: • Rifle_Brass_Collator_Plate_Large.stl • a large rifle brass collator plate for base down collation. • Rifle_Bullet_Collator_Plate_Large_#4.stl • a large rifle bullet collator plate for nose up/down collation that is to be used with a nose up/down #4 slide plate.
B | Slip_Clutch_8.5mm | This clutch is for pinned motor shafts that are 8.5mm or 10mm in diameter.
C | Slip_Clutch_Hex | This clutch is for motor shafts using hex couplers.
D | Slip_Clutch_Ring | This ring secures the slip clutch to the collator plate with 2 screws and nuts.
E | Collator_Plate_Handle | This handle allows for the ease of collator plate insertion/removal and mounts to the top of the collator plate with 2 screws; this is an optional part.

To prevent motor and/or collator plate damage during a jam, a slip clutch system has been implemented that interfaces with the motor shaft and collator plate. The slip clutch is secured to the collator plate with a pair of #6 x 1/2” screws and locknuts using parts B/C and D. In the event of a jam, the motor shaft will continue to rotate freely via the slip clutch system; here is a video (https://vimeo.com/517852664) of the slip clutch in action. The slip clutch system is compatible with a pinned 8mm motor shaft or a hex motor coupler. If a hex motor coupler is being used, be sure to grind the set screw so that it is flush with the coupler.

Bullets and brass with a base diameter <0.43” or >0.43” should use small or large collator plates, respectively; calibers like 300 Blackout (300BO) and FN 5.7 (5-7) have specific collator plates.

Custom collator plates for specific brass or bullet calibers can be made via the Collator Plate Generator.

## STEP 4 – SLIDE PLATES

Part | Layer Height | Infill | Supports | Walls | Adhesion
All | 0.12mm | 10-20% | None | 2 | None

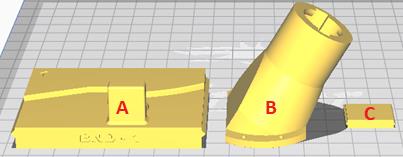
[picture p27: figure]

Slide Plates Folder
Part | STL File | Description
A X_Slide_Plate_X | | All files labelled Slide_Plate are used to create brass/bullet slide plates: • Bullet_Nose_Up_Slide_Plate_#7.stl • a ~.45 caliber bullet slide plate for nose up collation. • Brass_Slide_Plate.stl • a generic brass slide plate for base down collation.
B | Brass_X_Drop_Hole_Adapter | This adapter mounts to base up/down brass slide plates with 4 screws.
C | Brass_Slide_Adjuster | This adjuster allows for reliable brass collation of all calibers.

The drop hole plug must be used when collating base up/down brass and nose down bullets.

BRASS SLIDE PLATES
The brass slide plates are not caliber specific but do require some assembly. The brass slide adjuster has a slanted end which faces up and to the left of slide plate hole. Both drop hole adapters should face towards the collator when inserted into the slide plate housing. The following chart will assist in choosing the correct parts:
Brass Base Up Slide Plate | Brass Base Down Slide Plate
Brass_Base_Up_Slide_Plate_X | Brass_Slide_Plate
Brass_Base_Up_Drop_Hole_Adapter | Brass_Slide_Adjuster
Brass_Drop_Hole_Adapter

When collating base up brass, tilt the collator at an angle of 55-60 degrees for best results.

BULLET SLIDE PLATES
The bullet slide plates for nose up/down collation are caliber specific and are numbered, from #1 to #10, for bullets ranging from .22 to .50 caliber, respectively. The right side of these slide plates, called the ridge, decreases by 1mm as the slide plate number increases. In other words, slide plates #1 and #10 have ridge sizes of 14mm and 5mm, respectively. We have shared a spreadsheet (https://www.dropbox.com/sh/sz1o53q1a9hn4vn/AABjX7dSqZBSGDzpmdqG_ByAa/bullet%20compatibility%20chart.xlsx?dl=0) where community members can add their bullet caliber experiences with respective slide plate sizes. The slide plates we recommend are in the table to the right.
# | Caliber

2 .223
4 .308
5 9mm
7 .45 ACP
11 .300 BO

## STEP 5 – ADAPTERS

Part | Layer Height | Infill | Supports | Walls | Adhesion
All | 0.12mm | 10-20% | None | 2 | None

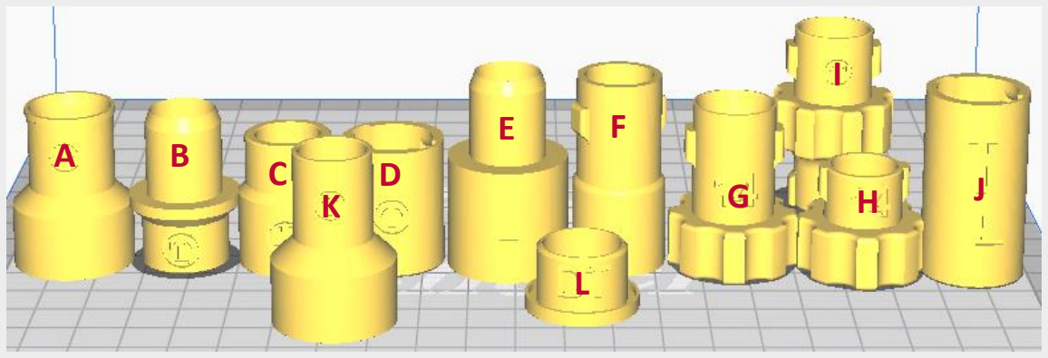
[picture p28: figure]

Adapters Folder
Part | STL File | Description
A | Dillon_Drop_Hole_Adapter | Dillon Casefeeder → A→ G
B | Dillon_Drop_Tube_Adapter | Dillon Case Feed Adapter → B → Drop Tube (bottom)
C | Dillon_Spring_Adapter | Dillon Case Feed Adapter → C → H
D | Dillon_Spring_Clear_Tube_Adapter | Dillon Clear Tube → D → H
E | Hornady_Drop_Tube_Adapter_X | Drop Tube → E → Hornady Bullet Feed Die
F | RCBS_Drop_Hole_Tube_Adapter_X | Drop Hole Adapter → F → RCBS Clear Tube → RCBS Bullet Feed Die
G | Spring_Adapter_X | Drop Hole Adapter → G → Spring Tube (top)
H | Spring_Adapter_X_DT | Spring Tube (bottom) → H → Drop Tube (top)
I | Drop_Hole_Drop_Tube_Adapter | Drop Hole Adapter → I → Drop Tube (top)
J | Spring_Drop_Tube_X | H → any part designed to fit on the bottom of a drop tube
K | Drop_Tube_Drop_Hole_X | Drop Tube (bottom) → G → Spring Tube → H → J → Bullet Feed Die
L | Drop_Tube_APP_Offset_Adapter | APP Offset Adapter → any part designed to fit on the bottom of a drop tube

Parts G and H are numbered according to the spring tube’s inner diameter
(ID); the outer diameter (OD) must not exceed the chart values to the right.
If the spring tube’s threads are reversed, mirror the z-axis in in Cura through the left icon, fourth from the top, and clicking the blue arrow.
Pre-mirrored | Post-mirrored
# | Spring ID | Spring OD

7 | 7mm (1/4”) | 9.5mm
8 | 8mm (5/16”) | 10.5mm
9 | 9mm | 11.5mm
10 | 10mm (3/8”) | 12.5mm
11 | 11mm | 13.5mm
12 | 12mm | 14.5mm
13 | 13mm (1/2”) | 15.5mm
14 | 14mm | 16.5mm

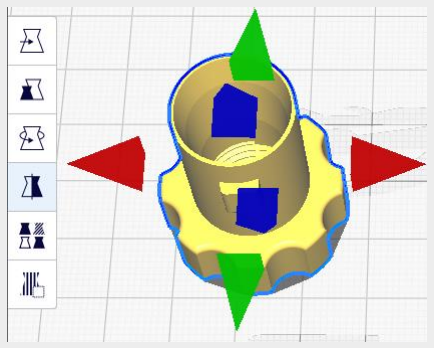
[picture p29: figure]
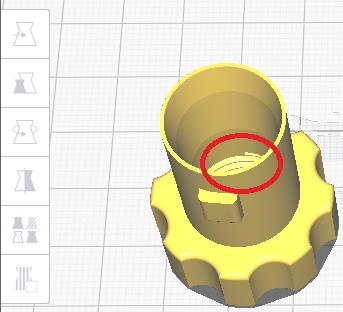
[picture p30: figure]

## STEP 6 – DROP TUBES

Part | Layer Height | Infill | Supports | Walls | Adhesion
Drop Tubes | 0.12mm | 10-20% | None | 2 | Brim
All Other | 0.12mm | 10-20% | None | 2 | None

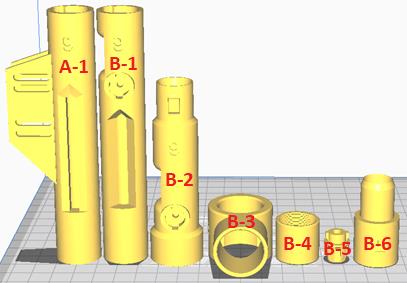
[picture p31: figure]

Drop Tubes Folder
Part | STL File | Description
A-1 | Switch_Drop_Tube_X | This drop tube is used for implementing the micro switch drop tube system.
B-1 | Drop_Tube_X | This drop tube is used to implement the photosensor or proximity sensor drop tube systems that connect directly to bullet feed dies.
B-2 | Drop_Tube_Alt_X | This drop tube is used to implement the photosensor or proximity sensor drop tube systems that connect directly to the collator.
B-3 | Drop_Tube_Proximity_Housing | This housing connects the proximity sensor to parts B-1 or B-2.
B-4 | Drop_Tube_Proximity_Thread_Insert | This insert threads over the proximity sensor and fits into part B-3.
B-5 | Drop_Tube_LED_Sensor_Knob | This quick attach knob housing fits over the photosensor and LED for quick connecting to parts B-1 or B-2.
B-6 | Drop_Tube_Spacer_X | These spacers fit on the bottom of parts B-1 or B-2 and should be used if light is bleeding through bullet noses; this an optional part.

The drop tubes are designed to work with both brass and bullets. Their bases are sized
to fit commercial bullet feed dies with an outer diameter of ~16.5mm, our bullet feed
dies and Lee APP accessories. The chart to the right shows which drop tube size is needed based on the base diameter of the brass and bullets being used.
# | Base Diameter

6 6.3mm
7 7.3mm
8 8.3mm
9 9.5mm
10 10.5mm
11 11.2mm
12 12.2mm
13 13.2mm

There are 3 drop tube systems to choose from, photosensor, proximity sensor and micro switch activated. All the systems are designed to stop the motor when a backlog of brass or bullets is detected to prevent jamming.

To connect a drop tube directly to the collator, connect parts B-2 with parts G, H and J, from Step 5, as follows: Drop Hole Adapter → B-2 → G → Spring Tube → H → J → Bullet Feed Die

THE PHOTOSENSOR DROP TUBE SYSTEM
This system uses a photosensor relay circuit and LED combo for backlog detection. One side of the drop tube houses an LED while the other houses a photosensor. Both are secured to the drop tube with quick connect sensor knobs, part B-5. If brass or bullets block the photosensor from detecting the LED’s light, the relay on the photosensor circuit activates and stops the motor. If bullet noses allow light to bleed through and prevent the motor from stopping, attach a drop tube spacer, part B-6, to the bottom of the drop tube to raise it by 8mm; the chart below shows which spacer will work with the drop tube number being used. Here are the required parts:
Drop Tube Mount
Drop_Tube_X
Drop_Tube_LED_Sensor_Knob
Drop_Tube_Spacer; this is an optional part.

THE PROXIMITY SENSOR DROP TUBE SYSTEM
This system uses a proximity sensor switch for backlog detection. We recommend using a 18mm diameter normally closed (NC) inductive proximity sensor with a minimum detection range of 8mm. As brass or bullets accumulate and approach the proximity sensor’s detection range, its switch will activate and stop the motor. Watch this video (https://vimeo.com/517852639) to understand how this system works and here are the required parts:
Drop Tube Mount
Drop_Tube_X
Drop_Tube_Proximity_Housing
Drop_Tube_Proximity_Thread_Insert

THE MICRO SWITCH DROP TUBE SYSTEM
This system uses a micro switch for backlog detection. The micro switch body attaches to the side of the drop tube while its switch arm protrudes into the drop tube itself. As brass or bullets begin to accumulate, the switch arm is tripped which stops the motor. Only parts labelled Switch_Drop_Tube_X are required for this system but ensure the 3D printer can do bridges of 15mm prior to printing; setting the parts cooling fan to 100% can help with bridging.
Drop Tube # | Drop Tube Spacer
6-7 | Small
8-10 | Medium
11-3 | Large

## STEP 7 – BULLET FEED DIES (OPTIONAL)

Part | Layer Height | Infill | Supports | Walls | Adhesion
All | 0.12mm | 10-20% | None | 2 | None

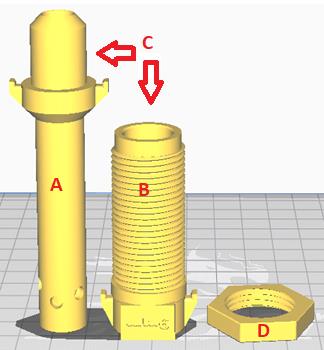
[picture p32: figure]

Bullet Feed Dies Folder
Part | STL File | Description
A | Feed_Die_X_Insert | This caliber specific bullet feed die insert slides into the bullet feed die main body and requires ball bearings and springs to operate.
B | Feed_Die_X_Body | This caliber specific bullet feed die main body threads directly into the toolhead.
C | Feed_Die_X_Set | A set of the above two parts for ease of printing
D | Lock_Ring | This lock ring fastens the bullet feed die to the toolhead.

A bullet feed die is composed of 2 parts and requires 3.5mm ball bearings and some elastic bands, hooked springs or O-rings. Using acetone on the inserts can help smooth them out and eliminate any friction issues. The inserts have 6 holes cut into them and are to be used with a pair of 3.5mm ball bearings. Use the upper holes for longer bullets and the lower holes for shorter bullets.

## STEP 8 – LEE APP ACCESSORIES (OPTIONAL)

Part | Layer Height | Infill | Supports | Walls | Adhesion
Base Slide | 0.12mm | 10-20% | 60˚ Overhang | 2 | None
Bullet Slide | 0.12mm | 10-20% | None | 2 | Raft
All Others | 0.12mm | 10-20% | None | 2 | None

A raft is needed for the bullet slides so that the spring pin, circled in red, is printed correctly.

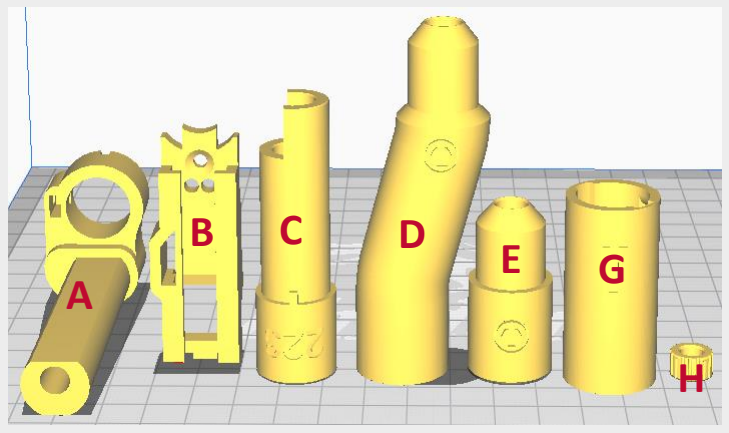
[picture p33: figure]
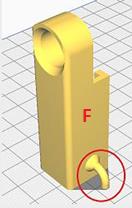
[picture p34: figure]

APP Folder
Part | STL File | Description
A APP_Bracket_Main | | This main bracket replaces the stock APP tube brackets allowing for usage of the quick caliber change system. Thread a ¼” nut between the press and bracket to achieve the proper height.
B | APP_Base_Slide | This base slide replaces the stock APP slide base for more reliable brass feeding; here is a video (https://vimeo.com/517851540) showing its assembly.
C | APP_X_Insert_X | This caliber specific brass/bullet insert allows for quick caliber changes.
D APP_Offset_Connector_X | | This offset connector comes in various sizes and is required if the APP handle is modified; (https://leeprecision.com/images/P/91629.jpg) this is an optional part otherwise.
E | APP_Drop_Tube_X_Adapter | This drop tube adapter allows for the usage of stock APP clear tubes with the quick caliber change system; this an optional part.
F APP_Bullet_Slide_X | | This caliber specific bullet slide replaces the stock APP slide for more reliable bullet feeding.
G APP_Spring_APP_Insert_X | | This caliber specific insert allows for the usage of spring tubes instead of stock APP clear tubes.
H | APP_Thumb_Screw | This thumb screw cover fits over the screw that secures the caliber specific brass/bullet inserts to the main bracket; this an optional part.

The offset connectors (OC) have inner diameters ranging from 6mm to 15mm whereas
the drop tubes range from 6mm to 13mm. Due to the bend in the OC, more space may
be required for ease of brass and bullet flow. If there are blockages, increase the OC size. The OC are designed to interface directly with stock Lee APP drop tubes and can
be matched up using the chart on the right:
The Lee APP accessories can be connected in the following 3 ways:
1. Main Bracket → Insert → OC → APP Drop Tube → APP Drop Tube Adapter → Drop Tube
2. Main Bracket → Insert → OC → Drop Tube
3. Main Bracket → Insert → APP Drop Tube → APP Drop Tube Adapter → Drop Tube
APP Tube # | OC #
1 6-7
2 8-10
3/4 | 11-15

## PARTS GENERATOR

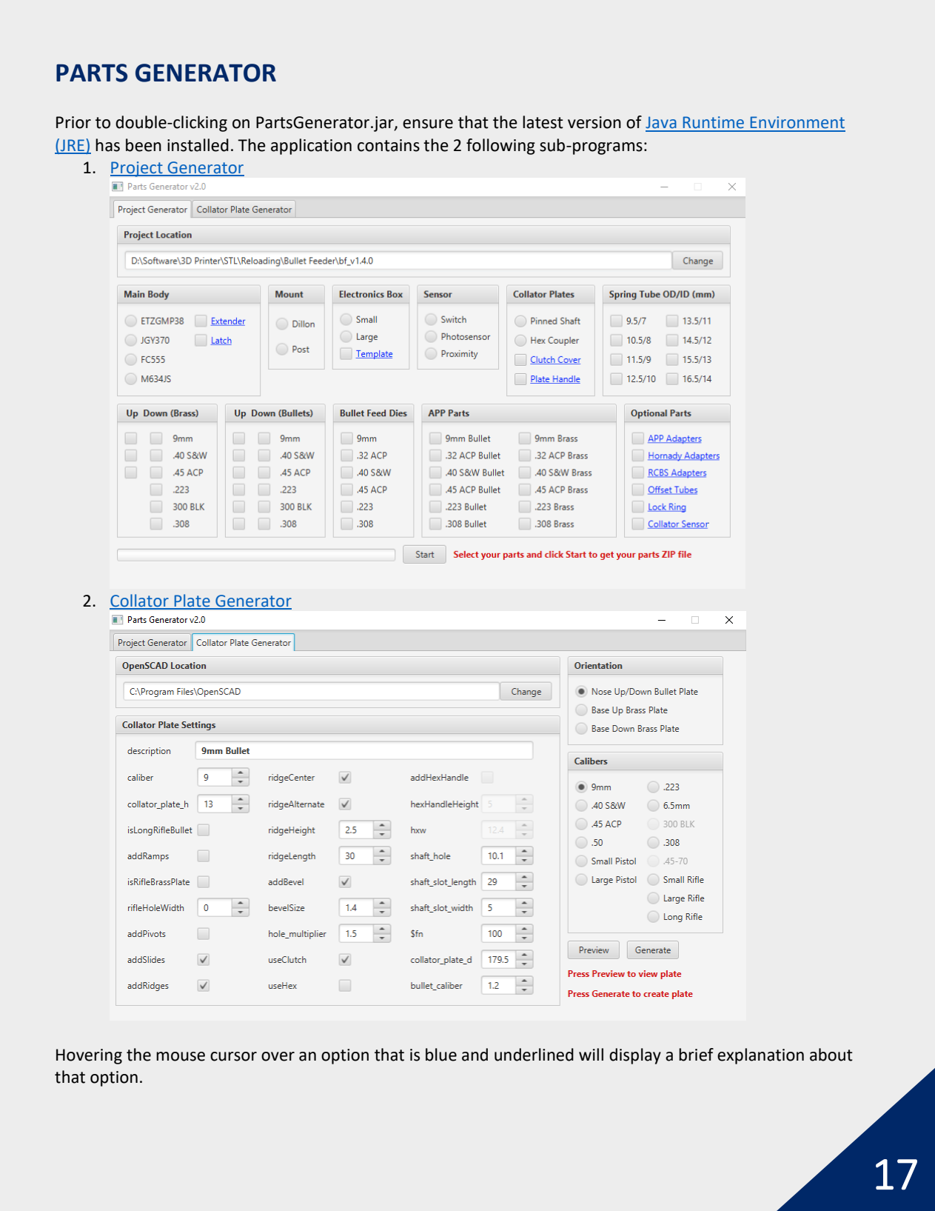
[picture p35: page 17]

Prior to double-clicking on PartsGenerator.jar, ensure that the latest version of Java Runtime Environment (JRE) (https://www.java.com/en/download/) has been installed. The application contains the 2 following sub-programs:
1. Project Generator
2. Collator Plate Generator

Hovering the mouse cursor over an option that is blue and underlined will display a brief explanation about that option.

## PROJECT GENERATOR

The first tab in the application is the Project Generator which collects the necessary STL part files to print.

The following steps explain how to use the Project Generator:
1. Ensure that Project Location is correct (see the above picture for reference)
2. Select the desired option(s)
3. Press the Start button
4. Wait for the ding sound to signal the completion of the process
5. Go to the main project folder and locate the newly created ZIP file called Parts.zip
6. Unzip Parts.zip to desired folder

The unzipped folder will have all the necessary STL part files and a file called Settings.pdf which will contain the recommended slicer settings for the parts.

## COLLATOR PLATE GENERATOR

The second tab in the application is the Collator Plate Generator which creates custom collator plates.

Ensure that OpenSCAD (https://www.openscad.org/) is installed prior to using this feature. The default installation folders are as follows:
- C:\Program Files (x86)\OpenSCAD – for a 32-bit installation
- C:\Program Files\OpenSCAD – for a 64-bit installation

The following steps explain how to use the Collator Plate Generator:
1. Ensure that OpenSCAD Location is correct (see the above picture for reference)
2. Select the desired brass/bullet orientation
3. Select the desired caliber
4. Modify the settings on the left (optional step)
5. Press the Preview button to view the plate (optional step)
6. Press the Generate button to create; this can be a very long process but can be cancelled
7. Wait for the ding sound to signal the completion of the process
8. Go to the main project folder and locate the newly created collator plate file

Alternatively, custom collator plates can be created directly from OpenSCAD by double-clicking on the .scad file located in the Collator Plates sub-folder of the main project folder. When the program starts, there will be an editor on the left side and a 3D rendering of a collator plate on the right. If the editor is not visible, uncheck the “Hide editor” option in the View menu item. Instructions for creating the plate can be found on the very top of the editor window.

Descriptions and recommendations of all the collator plate settings can be found on the next few pages.

SETTINGS OVERVIEW

Here is a description of all the adjustable settings; all measurements are in millimetres (mm):
Setting | Description
description | Sets the text that will appear on the top of collator plate.
caliber | Sets the hole size (caliber) for the collator plate.
collator_plate_h | Sets the desired height of the collator plate.
isLongRifleBullet | Signifies that a long rifle bullet collator plate is being created.
addRamps | Adds ramps to the holes for better long bullet feeding.
isRifleBrassPlate | Signifies that a rifle brass collator plate is being created.
rifleHoleWidth | Sets the hole size according to the width of the rifle brass.
addPivots | Adds pivots for base down brass collation.
addSlides | Adds slides to the top of the collator plate for nose up/down bullet collation.
addRidges | Adds ridges to the top of the collator plate for base up/down brass collation.
ridgeCenter | Sets the ridge to align with hole center, otherwise it aligns with far side of hole.
ridgeAlternate | Adds ridges to every other hole.
ridgeHeight | Sets the height of the ridges.
ridgeLength | Sets the length of the ridges.
addBevel | Adds a bevel to the top of the holes.
bevelSize | Sets the size of the top bevels; use values between 1.3 and 1.6
hole_multiplier | Sets the number of holes using this multiplier.
useClutch | Adds a circular cut out to the center of the plate for a slip clutch.
useHex | Adds a hex shape cut out to the center of the plate for a hex motor coupler.
addHexHandle | Adds a handle to the top of the hex shape for easy plate lifting.
hexHandleHeight | Sets the height of the hex handle.
hxw | Sets the width of the hex shape cut out.
shaft_hole | Sets the diameter of the motor shaft hole.
shaft_slot_length | Sets the length of the motor shaft pin.
shaft_slot_width | Sets the width of the motor shaft pin.
$fn | Sets the resolution of the plate; use values between 50 and 100
collator_plate_d | Sets the diameter of the plate; AmmoMike83 plates are 147.5
bullet_caliber | Adds an offset amount to each hole for oversized bullets; use values between 1 and 1.5

BRASS COLLATOR PLATE SETTINGS

Here is a table of recommended settings for caliber specific and generic base up/down brass collator plates:
Setting | Base Down | Base Up
9 | .40 | Pistol Small | .45 | .50 | Pistol Large | .300 | Small Rifle | .45-70 | Large Rifle | Small Pistol | Large Pistol
description | Enter the text to appear on the top of the bullet collator plate.
caliber | 9 | 10.2 | 12 | 11.5 | 12.7 | 15 | 36 | 46 | 56 | 54 | 10.5 | 12.5
collator_plate_h | 7 | | | 8 | | | | | | | 20 | 22
isLongRifleBullet | false
addRamps | false
isRifleBrassPlate | false | | | | | | true | | | | false
rifleHoleWidth | 0 | | | | | | 9 | | 12 | | 0
addPivots | false | | | | | | | | | | true
addSlides | false
addRidges | true
ridgeCenter | true
ridgeAlternate | true
ridgeHeight | 2.5
ridgeLength | 30
addBevel | false | | | | | | | | | | true
bevelSize | 1.6
hole_multiplier | 1.5
useClutch | true/false; this is an optional setting
useHex | true/false; this is an optional setting
addHexHandle | true/false; this is an optional setting
hexHandleHeight | 5
hxw | 12.4
shaft_hole | 10.1
shaft_slot_length | 29
shaft_slot_width | 5
$fn | 100
collator_plate_d | 180
bullet_caliber | 1.2

BULLET COLLATOR PLATES SETTINGS

Here is a table of recommended settings for caliber specific and generic nose up/down bullet collator plates:
Setting | 9 | .40 | .45 | .50 | Small Pistol | Pistol Large | .223 | 6.5 | .308 | Small Rifle | Large Rifle | Long Rifle
description | Enter the text to appear on the top of the brass collator plate.
caliber | 9 | 10.2 | 11.5 | 12.7 | 9 | 11.5 | 5.69 | 6.72 | 7.82 | 5.7 | 7.82 | 7.82
collator_plate_h | 13 | | | | | | 18 | | | | | 22
isLongRifleBullet | false | | | | | | | | | | | true
addRamps | false | | | | | | | | | | | true
isRifleBrassPlate | false
rifleHoleWidth | 0
addPivots | false
addSlides | true
addRidges | true
ridgeCenter | true
ridgeAlternate | true | | | | | | | | | | | false
ridgeHeight | 2.5 | | | | | | | | | | | 3
ridgeLength | 30 | | | | | | | | | | | 10
addBevel | true
bevelSize | 1.4
hole_multiplier | 1.5 | | | | | | | | | | | 3
useClutch | true/false; this is an optional setting
useHex | true/false; this is an optional setting
addHexHandle | true/false; this is an optional setting
hexHandleHeight | 5
hxw | 12.4
shaft_hole | 10.1
shaft_slot_length | 29
shaft_slot_width | 5
$fn | 100
collator_plate_d | 180
bullet_caliber | 1.2

## APPENDIX

## COLLATOR WIRING

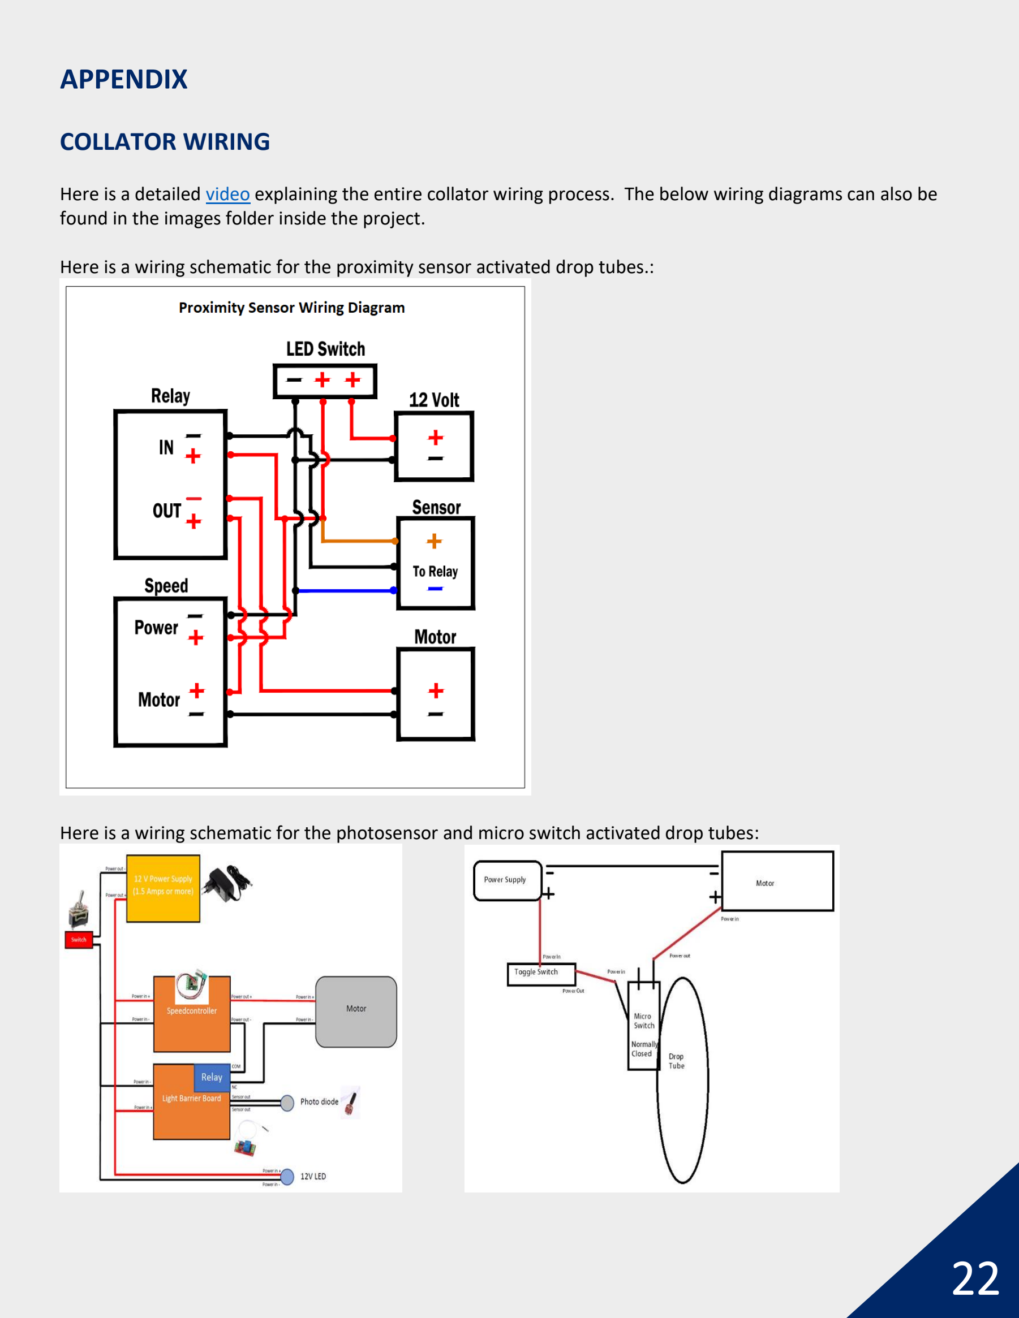
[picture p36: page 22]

Here is a detailed video (https://www.youtube.com/watch?v=oS00VdU-N3Y&t=233s&ab_channel=hillsgun) explaining the entire collator wiring process. The below wiring diagrams can also be found in the images folder inside the project.

Here is a wiring schematic for the proximity sensor activated drop tubes.:

Here is a wiring schematic for the photosensor and micro switch activated drop tubes:

Proximity Sensor Wiring:

1. 12v - comes off the 12 volt power source and goes to everything except the relay and the motor. (sensor - is blue)
2. 12v + comes off 12 volt and goes to switch.
3. 12v + comes off the switch and goes to everything except the motor. (sensor + is brown) (relay pin 2)
4. 12v + goes from the speed controller out to the relay pin 4.
5. 12v + goes from relay pin 3 to the motor +.
6. 12v - goes from the speed controller out to the motor -.
7. 12v - goes from sensor signal - (black wire) to relay - in (pin 1)

## TROUBLESHOOTING

1. My parts are not sticking to the print bed.
There are multiple causes and remedies for this situation. Try the following steps one at a time:
i. thoroughly clean the bed with isopropyl alcohol
ii. ensure the bed is level
iii. check the print nozzle height; first layers should look “squished”
iv. increase print and/or bed temperature in small increments
v. use a brim or a raft
vi. add a small amount of Elmer’s Purple Glue Stick (https://www.amazon.com/Elmers-Disappearing-Purple-School-E562/dp/B00143SNPG) to help with adhesion
2. My prints are not coming out accurate and/or have defects in them.
Try the following steps one at a time:
i. make sure the printer is calibrated according to the 3D PRINTER section
ii. check to make sure the recommended print settings are being used
iii. try a different brand of filament; we recommend Hatchbox, Overture, Sunlu, E-Sun, AMZ3D, … etc.
3. My collator is jamming and/or not collating correctly.
Try the following steps one at a time:
i. ensure the correct parts are being using
ii. increase or decrease motor speed
iii. increase or decrease collator tilt
iv. adjust the slide plate further out by adding a screw to the hole on the rear of the plate
4. The spring pin on the bullet slide is not adhering to the bed and/or breaks off during printing.
The bullet slide can be tricky to print due to the small surface are of the bevelled spring pin which contacts the bed. Therefore, we recommend printing it with a raft using the following settings:

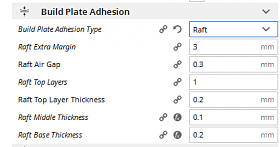
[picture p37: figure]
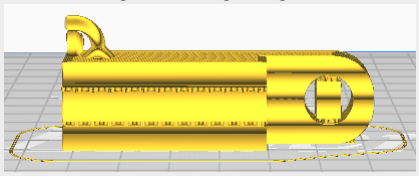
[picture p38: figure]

If the raft doesn’t work, print the bullet slide on its side and ensure that the Everywhere option is selected in the Support Placement setting as shown in the above picture.

## LICENSE

This work is licensed under the Creative Commons Attribution-NonCommercial 4.0 International License.

You are free to:
- Share — copy and redistribute the material in any medium or format
- Adapt — remix, transform, and build upon the material

Under the following terms:
- Attribution — You must give appropriate credit, provide a link to the license, and indicate if changes were made. You may do so in any reasonable manner, but not in any way that suggests the licensor endorses you or your use.
- NonCommercial — You may not use the material for commercial purposes.
- No additional restrictions — You may not apply legal terms or technological measures that legally restrict others from doing anything the license permits.

To view a copy of this license, visit http://creativecommons.org/licenses/by-nc/4.0/

or send a letter to:
Creative Commons, PO Box 1866, Mountain View, CA 94042, USA.

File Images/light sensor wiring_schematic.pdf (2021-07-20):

# Basic schematic with light barrier board

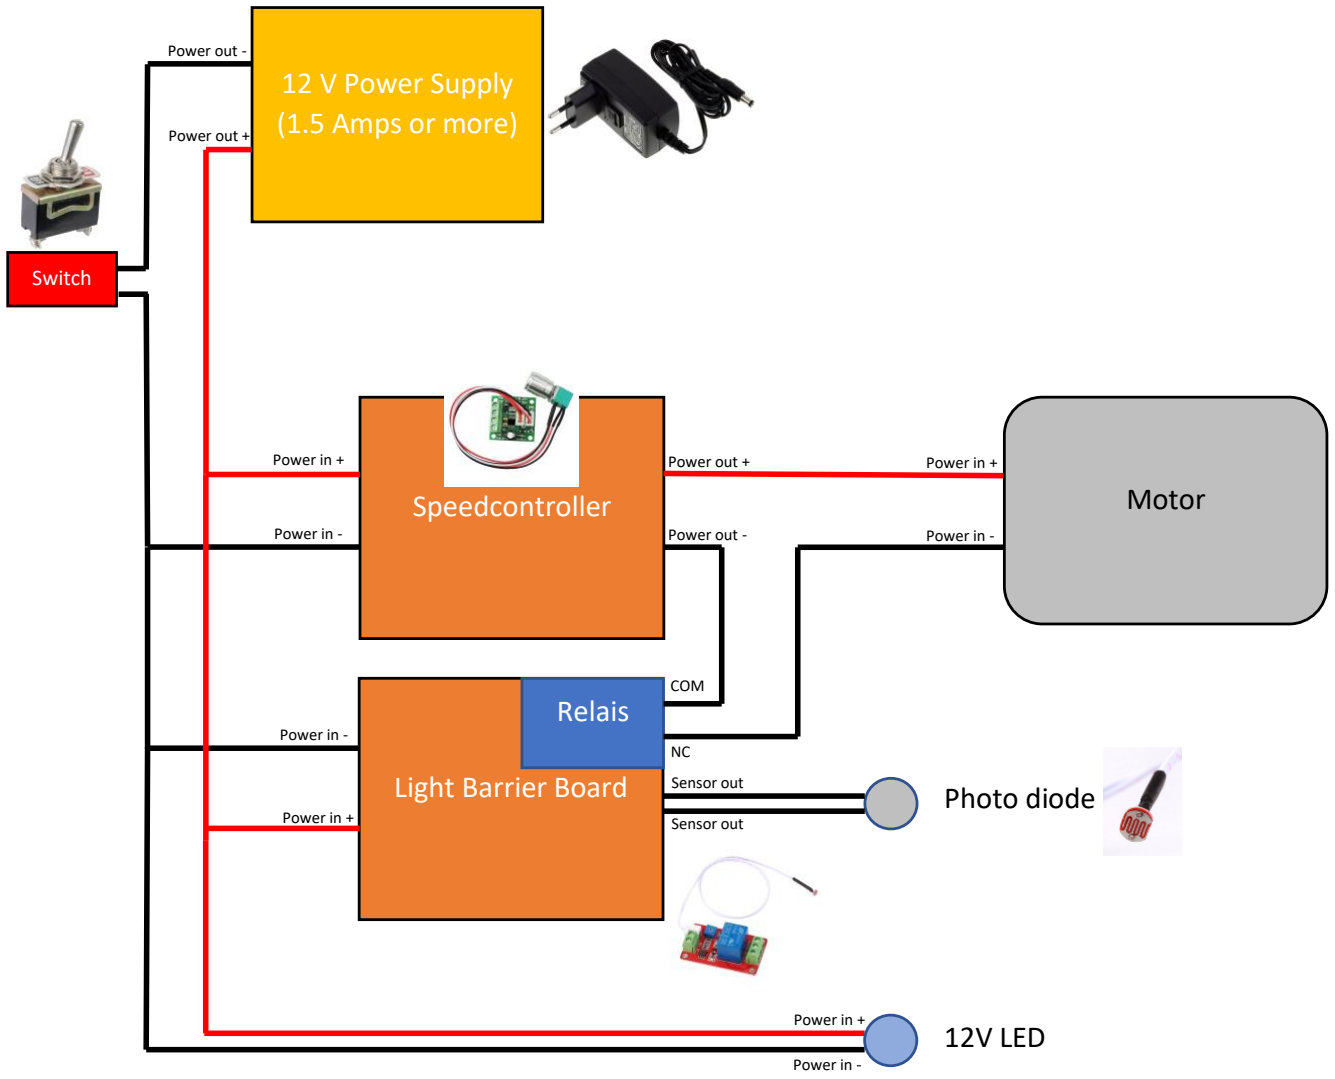
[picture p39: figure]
Motor Speedcontroller; 12 V Power Supply (1.5 Amps or more); Light Barrier Board; Photo diode; Relais; 12V LED; COM; Power out +; Power out -; Power in +; Power in -; Sensor out; Switch

# Basic schematic with micro switch

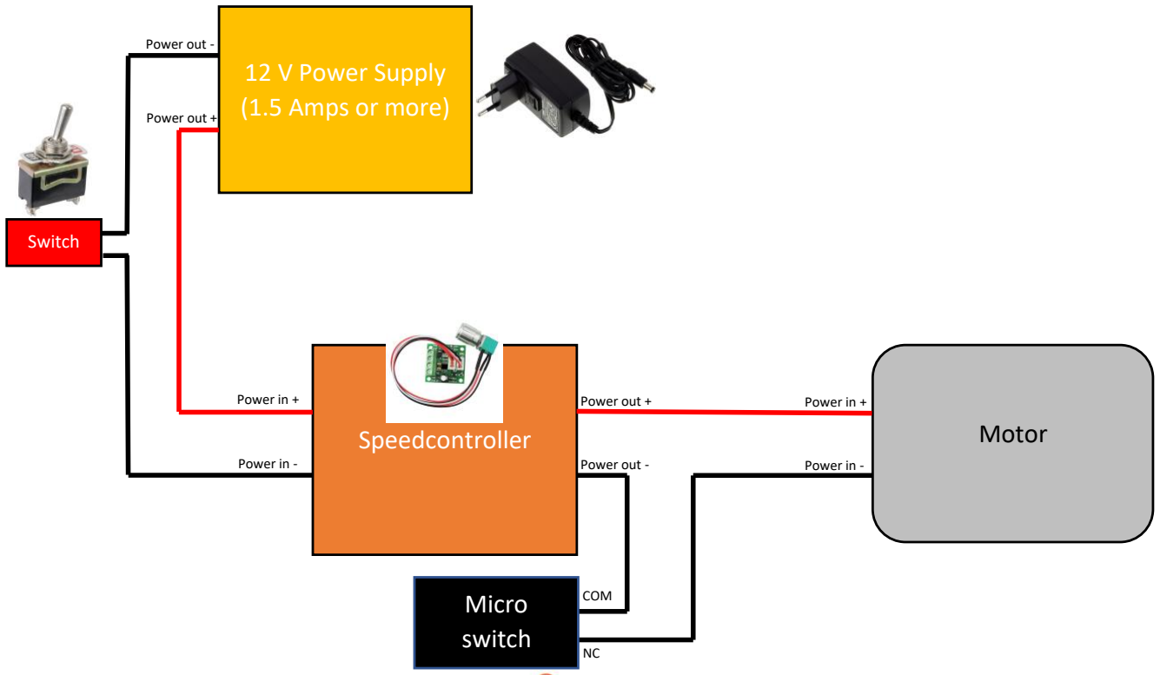
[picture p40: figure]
Motor Speedcontroller; 12 V Power Supply (1.5 Amps or more); COM; Power out +; Power out -; Power in +; Power in -; Switch; Micro switch

# Additional information

# Speed Controllor detailed wiring diagram

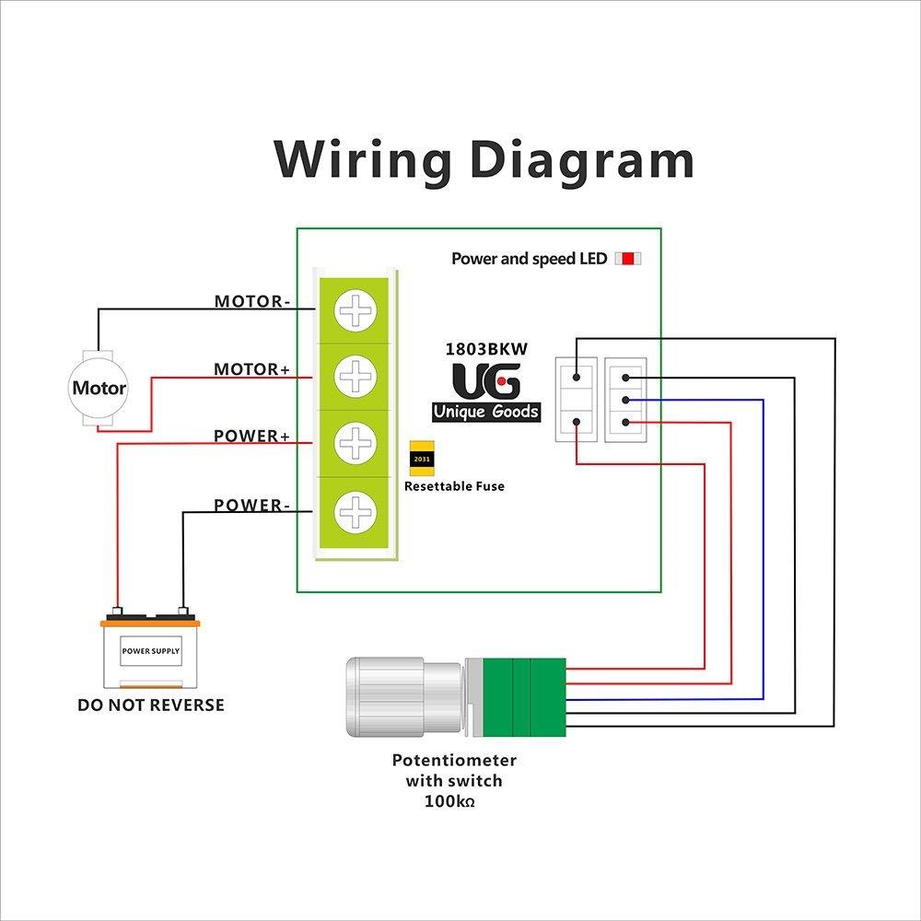
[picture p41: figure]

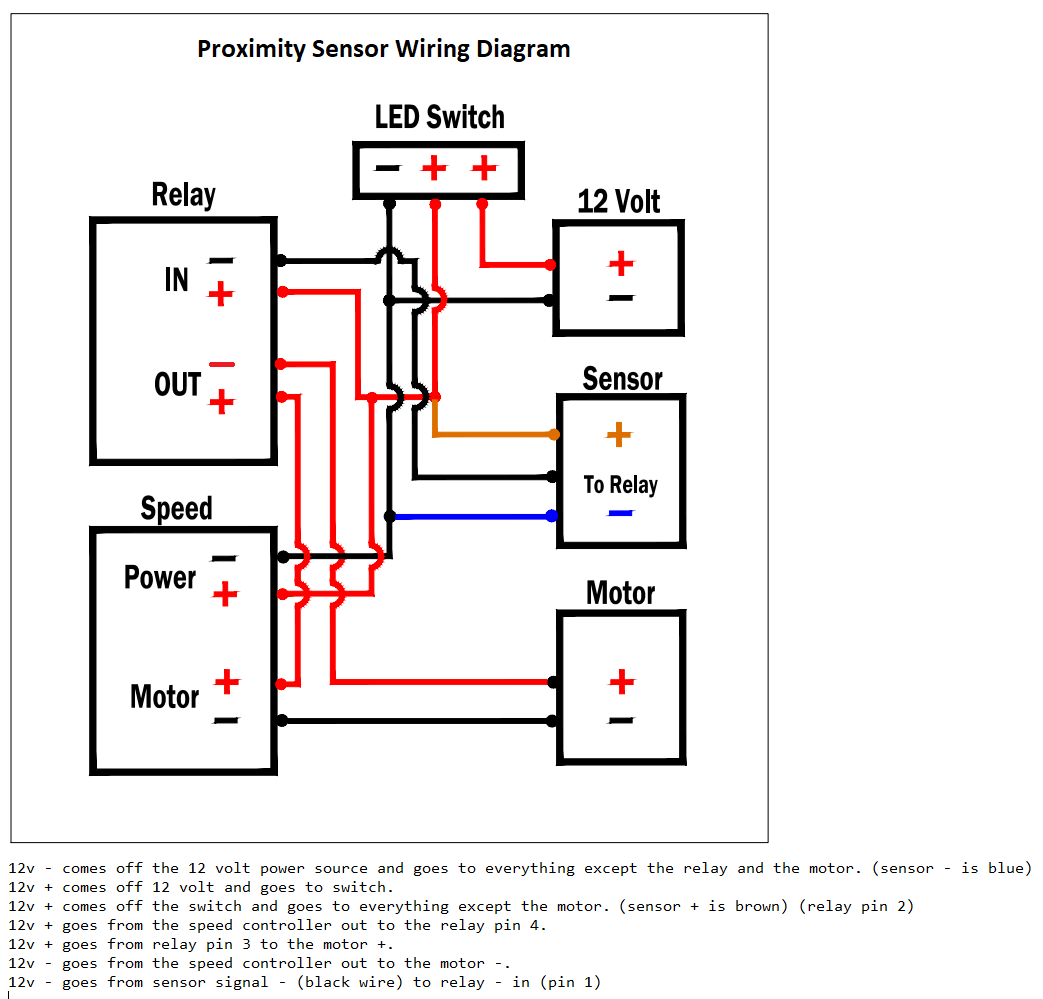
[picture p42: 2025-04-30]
Images/Proximity Wiring Schematic.png

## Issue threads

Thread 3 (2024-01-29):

OpenSCAD Files and Mount Square Tube

MHBatGH, 2024-01-29:
Hello,

is it possible to get the OpenSCAD files? I would like to modify the file so that it works with 30mm aluminum profile rail.
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

MHBatGH, 2024-02-03:
Please add this file to your repository
[Mount_Post-30mm-Profile-20240203-1.zip](https://github.com/BF556/Feeder/files/14154371/Mount_Post-30mm-Profile-20240203-1.zip)

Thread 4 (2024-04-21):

Main components as STEP files

kzkv, 2024-04-21:
Hi, I'm working on several projects utilizing the feeder. I would appreciate it if you had components of the system available as STEP files so I can mate the assembly parts in Solidworks and avoid working back from the .stl mesh. The larger models (main body, plates) would be the most helpful if you could provide only a subset of the files.

Thank you!
